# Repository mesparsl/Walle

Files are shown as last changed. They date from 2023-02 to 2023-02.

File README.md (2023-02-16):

# Walle
El wall-e es nuestro proyecto final nos hemos basado en este wall-e que encontramos por internet https://3dwork.io/wall-e-replica-impresion-3d/
!

[image](https://user-images.githubusercontent.com/124558681/219344904-b29a2cb5-0929-498d-a3b3-13a339d1f519.png)







1. Código Arduino (wall-e)

Programa principal para controlar los motores y servos del robot. Las características incluyen:

Una cola de animación, que realiza un seguimiento de los próximos movimientos de servo que el robot debe realizar.

Un generador de movimiento aleatorio, que permite que el robot se mueva de forma autónoma y parezca animado.

Control de velocidad de todos los servomotores, facilitando aceleraciones y desaceleraciones suaves.

Análisis en serie sin bloqueo, que permite el control remoto de los movimientos del robot.

Supervisión del nivel de la batería mediante un circuito divisor de potencial.

2. Servidor web Raspberry Pi (interfaz_web)

La interfaz web está programada en Python y utilizaMatraz para generar un servidor. La Raspberry Pi se conecta a través de USB al microcontrolador Arduino. Las características principales son:

Un joystick JavaScript, con el que se puede controlar fácilmente el movimiento del robot.

Control manual de todos los servomotores.

Una lista de animaciones de movimiento que puede realizar el robot.

Una lista de sonidos que se pueden reproducir.

Página de configuración, donde se pueden modificar los parámetros del motor, el volumen del sonido y las opciones de video.

Soporte para mando de juegos; en cualquier navegador moderno, puede usar un controlador Xbox o PlayStation conectado para controlar el robot.

Una página de inicio de sesión simple para evitar que todos tengan acceso a los controles (nota: este no es un sistema de control de acceso completo, no use esta interfaz web en redes públicas/no confiables)
 
 Imagen de la interfaz web y el robot. 
 
Instrucciones de configuración

1.Arduino

[a] Instalación básica

Asegúrese de que el cableado de la electrónica coincida con el diagrama que se muestra a continuación.

Descarga/clona la carpeta "wall-e" del repositorio de GitHub.

Abierto wall-e.ino en el IDE de Arduino; Los archivos animaciones.ino, MotorController.hpp y Cola.hpp también debería abrirse automáticamente en pestañas separadas del IDE.

Instala el Adafruit _ PWM Servo Driver.h biblioteca

Vaya a Sketch -> Incluir biblioteca -> Administrar bibliotecas...

BuscarServidor de Adafruit.

Instale la última versión de la biblioteca.

Conéctese a la computadora al microcontrolador con un cable USB. Asegúrese de que la correcta Junta y Puerto se seleccionan en el Herramientas menú.

Cargue el boceto en el microcontrolador.

Diagrama que muestra el cableado de los componentes electrónicos del robot.

[b] Prueba del programa principal



Una vez que el boceto se haya cargado en el Arduino, encienda la batería de 12 V mientras el microcontrolador aún está conectado a la computadora.

Abre el monitor de serie (botón en la parte superior derecha de Arduino IDE). Establezca la velocidad en baudios en 115200.

Para controlar el movimiento del robot, envía los caracteres 'w', 'a', 's' o 'd' para avanzar, izquierda, atrás o derecha respectivamente. Envía 'q' para detener todo movimiento.

Para mover la cabeza, envía los caracteres 'j', 'l', 'i' o 'k' para inclinar la cabeza hacia la izquierda o hacia la derecha y los ojos hacia arriba o hacia abajo. En esta etapa, los servos pueden intentar moverse más de lo debido y pueden parecer descoordinados. Esto se resolverá realizando los pasos de calibración del servomotor a continuación.

[c] Calibración del servomotor

Descarga/clona la carpeta "wall-e_calibration" del repositorio de GitHub

Abierto wall-e_calibration.ino en el IDE de Arduino.

Cargue el boceto en el microcontrolador, abra el monitor serie y establezca la velocidad de transmisión en 115200.

El esquema se usa para calibrar las longitudes de pulso PWM máximas y mínimas requeridas para mover cada servomotor en su rango de movimiento deseado. Las posiciones estándar BAJA y ALTA de cada uno de los servos se pueden ver en los diagramas en mi sitio web.

Al iniciar el boceto y abrir el monitor serie, debe aparecer un mensaje después de 2-3 segundos, diciendo que está listo para calibrar la posición BAJA del primer servomotor (la rotación del cabezal).

Envía el carácter 'a' y 'd' para mover el motor hacia adelante y hacia atrás en -10 y +10. Para un control más preciso, utilice los caracteres 'z' y 'c' para mover el motor en -1 y +1.

Una vez que el motor esté en la posición correcta, envíe el carácter 'n' para continuar con el paso de calibración. Pasará a la posición ALTA del mismo servo, después de lo cual el proceso se repetirá para cada uno de los 7 servos del robot.

Cuando todas las articulaciones estén calibradas, el boceto generará una matriz que contiene los valores de calibración en el monitor en serie.

Copie la matriz y péguela en lineas 144 al 150 del programawall-e.ino. La matriz debería verse similar a esto:



2. Servidor web Raspberry Pi

[a] Instalación básica

Configure Raspberry Pi para ejecutar la última versión de Raspberry Pi OS (Raspbian) - Full. Las instrucciones de configuración se pueden encontrar en el sitio web de frambuesa pi.

Abra la terminal de línea de comandos en la Raspberry Pi.

Asegúrese de que la lista de paquetes se haya actualizado (esto puede llevar algún tiempo):sudo apt update

Instalar Matraz - este es un marco de Python utilizado para crear servidores web:

Asegúrese de que pip esté instalado:sudo apt-get install python3-pip

Instale Flask y sus dependencias:sudo apt-get install python3-flask

sudo apt install git libsdl1.2-dev

sudo apt install git libsdl-mixer1.2-dev

sudo pip3 instalar pygame pyserial

Clone el repositorio en el directorio de inicio de Raspberry Pi:

cd ~
git clone https://github.com/chillibasket/walle-replica.git

Configure la contraseña del servidor web:

nano ~/walle-replica/web_interface/app.py

En línea26 deapp.py donde esta dice put_password_here, inserte la contraseña que desea utilizar para la interfaz web.

(Opcional) Cambie el directorio de audio predeterminado y la ubicación de la secuencia de comandos utilizada para iniciar/detener la transmisión de video.

Si siguió exactamente los pasos anteriores, no hay necesidad de hacerlo. Sin embargo, si desea mover los archivos de la interfaz web a un directorio diferente en Raspberry Pi, deberá cambiar la ubicación donde el programa buscará los archivos de audio.

En línea29 de app.py, escriba el directorio donde se encuentran los archivos de audio. Asegúrese de que la ubicación del directorio termine con una barra diagonal:/.

En línea28 de app.py, se puede modificar la ubicación del script utilizado para iniciar y detener la transmisión de la cámara de video.

Conéctese al Arduino/microcontrolador:

Conecte el Arduino/microcontrolador al puerto USB de la Raspberry Pi.

Si desea que el puerto serie utilizado por Arduino se seleccione de forma predeterminada en la interfaz web, puede configurar un dispositivo de puerto serie preferido en el código. ir a la línea27 deapp.py y reemplace el texto "ARDUINO" con el nombre de su dispositivo. El nombre debe coincidir con el que aparece en el menú desplegable en la pestaña "Configuración" de la interfaz web.

Para hacer que la interfaz se conecte automáticamente al Arduino cuando se inicia, puede cambiar la línea31 aautoStartArduino = Verdadero

Prensa CTRL+O para ahorrar yCTRL + X para salir del editor nano.

[b] Uso del servidor web

Para determinar la dirección IP actual de Raspberry Pi en su red, escriba el comando: hostname -I

Para iniciar el servidor:python3 ~/walle-réplica/web_interface/app.py

Para acceder a la interfaz web, abra un navegador en cualquier computadora/dispositivo en la misma red y escriba la dirección IP de la Raspberry Pi, siga por:5000. Por ejemplo192.168.1.10:5000

Para detener el servidor presione:CTRL + C

Para comenzar a controlar el robot, primero debe iniciar la comunicación en serie con el Arduino. Para ello, acceda a laAjustes pestaña de la interfaz web, seleccione el puerto serie correcto de la lista desplegable y presione en elreconectar botón.







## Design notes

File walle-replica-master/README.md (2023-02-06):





# Wall-E Robot Replica
Robot and controller code for a Wall-E replica robot. For more information about the robot, visit https://wired.chillibasket.com/3d-printed-wall-e/

<br />
<br />

## 1. Arduino Code (wall-e)
Main program to control the motors and servos of the robot. Features include:
1. An animation queue, keeping track of the next servo movements the robot needs to perform.
1. A random movement generator, allowing the robot to autonomously move and appear animated.
1. Velocity control of all servo motors, facilitating smooth accelerations and decelerations. 
1. Non-blocking serial parsing, allowing the movements of the robot to be remote controlled.
1. Battery level monitoring using a potential divider circuit.
<br />

## 2. Raspberry Pi Web Server (web_interface)
The web interface is programmed in Python and uses *Flask* to generate a server. The Raspberry Pi is connected via USB to the Arduino micro-controller. The main features are:
1. A JavaScript joystick, with which the movement of the robot can easily be controller.
1. Manual control of all the servo motors.
1. A list of movement animations which can be performed by the robot.
1. A list of sounds which can be played.
1. Settings page, where motor parameters, sound volume, and video options can be modified.
1. Gamepad support; on any modern browsers, you can use a connected Xbox of PlayStation controller to control the robot.
1. A simple login page to prevent everyone from having access to the controls (note: this is not a full access control system, please don't use this web interface on untrusted/public networks)

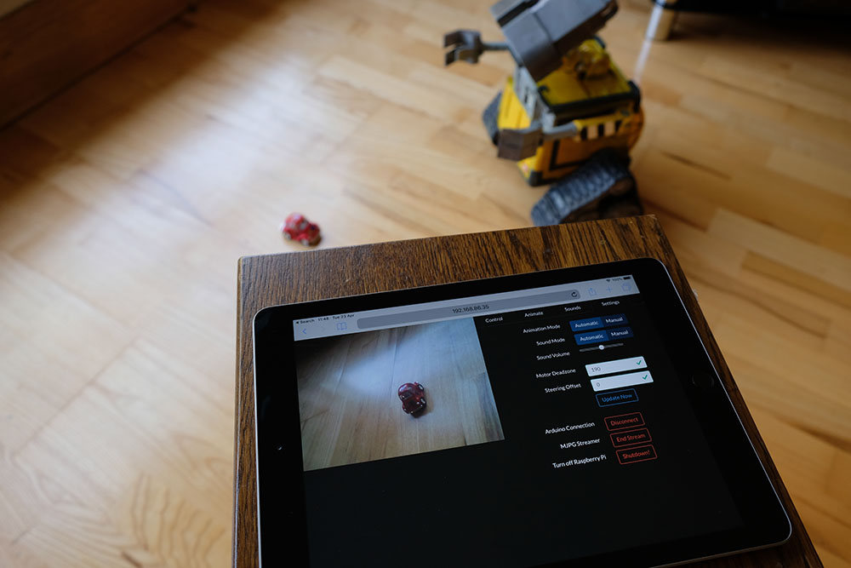
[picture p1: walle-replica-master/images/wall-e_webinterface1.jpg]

*Image of the web interface and robot*

<br />
<br />

## Setup Instructions

### 1. Arduino

#### [a] Basic Installation
1. Ensure that the wiring of the electronics matches the diagram shown below.
1. Download/clone the folder "wall-e" from the GitHub repository.
1. Open `wall-e.ino` in the Arduino IDE; the files `animations.ino`, `MotorController.hpp` and `Queue.hpp` should automatically open on separate tabs of the IDE as well.
1. Install the `Adafruit_PWMServoDriver.h` library
	1. Go to Sketch -> Include Library -> Manage Libraries...
	1. Search for *Adafruit Servo*.
	1. Install latest version of the library.
1. Connect to the computer to the micro-controller with a USB cable. Ensure that the correct *Board* and *Port* are selected in the *Tools* menu.
1. Upload the sketch to the micro-controller.

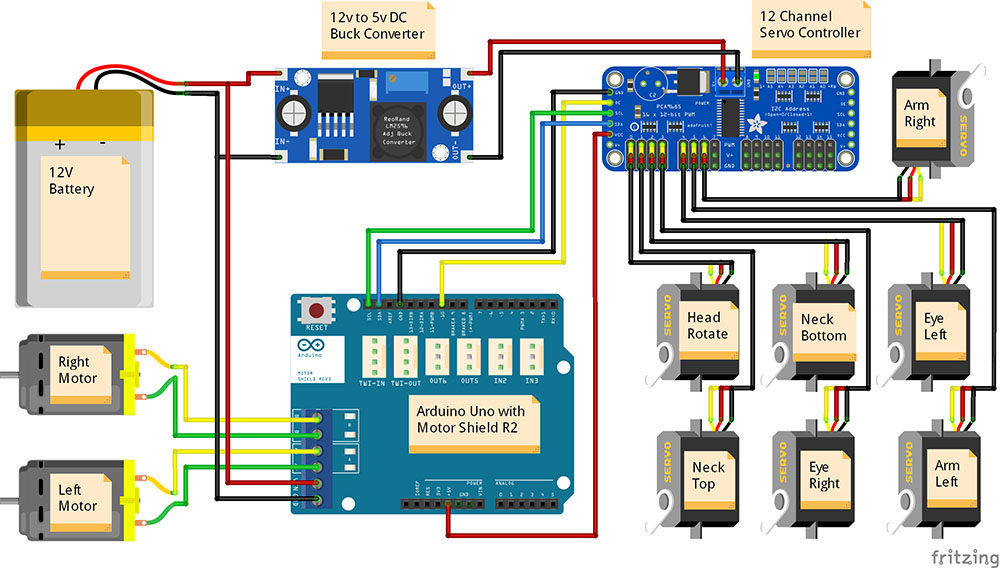
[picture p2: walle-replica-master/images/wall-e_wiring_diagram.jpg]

*Diagram showing the wiring of the robot's electronic components*
<br />

<br />

#### [b] Testing the Main Program
1. Once the sketch has been uploaded to the Arduino, power on the 12V battery while the micro-controller is still connected to the computer.
1. Open the *Serial Monitor* (button in top-right of Arduino IDE). Set the baud rate to 115200.
1. To control the movement of the robot, send the characters 'w', 'a', 's' or 'd' to move forward, left, back or right respectively. Send 'q' to stop all movement.
1. To move the head, send the characters 'j', 'l', 'i' or 'k' to tilt the head left or right and the eyes upwards or downwards. At this stage, the servos may try to move further than they should and may look uncoordinated. This will be solved by performing the servo motor calibration steps below.

<br />

#### [c] Servo Motor Calibration
1. Download/clone the folder "wall-e_calibration" from the GitHub repository
1. Open `wall-e_calibration.ino` in the Arduino IDE.
1. Upload the sketch to the micro-controller, and open the serial monitor and set the baud rate to 115200.
1. The sketch is used to calibrate the maximum and minimum PWM pulse lengths required to move each servo motor across its desired range of motion. The standard LOW and HIGH positions of each of the servos can be seen on diagrams [on my website](https://wired.chillibasket.com/3d-printed-wall-e/). 
1. When starting the sketch and opening the serial monitor, the a message should appear after 2-3 seconds, saying that it is ready to calibrate the LOW position of the first servo motor (the head rotation).
1. Send the character 'a' and 'd' to move the motor backwards and forwards by -10 and +10. For finer control, use the characters 'z' and 'c' to move the motor by -1 and +1. 
1. Once the motor is position in the correct position, send the character 'n' to proceed to the calibration step. It will move on to the HIGH position of the same servo, after which the process will repeat for each of the 7 servos in the robot.
1. When all joints are calibrated, the sketch will output an array containing the calibration values to the serial monitor.
1. Copy the array, and paste it into [lines 144](https://github.com/chillibasket/walle-replica/blob/master/wall-e/wall-e.ino#L144) to 150 of the program *wall-e.ino*. The array should look similar to this:
    ```cpp
    int preset[][2] =  {{410,120},  // head rotation
                        {532,178},  // neck top
                        {120,310},  // neck bottom
                        {465,271},  // eye right
                        {278,479},  // eye left
                        {340,135},  // arm left
                        {150,360}}; // arm right
    ```

<br />

#### [d] Battery Level Detection (Optional)
When using batteries to power the robot, it is important to keep track of how much power is left. Some batteries may break if they are over-discharged, and the SD card of the Raspberry Pi may become corrupted if not enough power is delivered.
1. To use the battery level detection feature on the Arduino, connect the following resistors and wiring as shown in the image below. The resistors (potential divider) reduce the 12V voltage down to a value below 5V, which is safe for the Arduino to measure using its analogue pins. The recommended resistor values are `R1 = 100kΩ` and `R2 = 47kΩ`.
1. Uncomment [line 54](https://github.com/chillibasket/walle-replica/blob/master/wall-e/wall-e.ino#L54) `#define BAT_L` in the main Arduino sketch *wall-e.ino*.
1. If you are using different resistor values, change the value of the potential divider gain factor on line 54 of the sketch, according to the formula: `POT_DIV = R2 / (R1 + R2)`. 
1. The program should now automatically check the battery level every 10 seconds, and this level will be shown on the Raspberry Pi web-interface in the "Status" section.

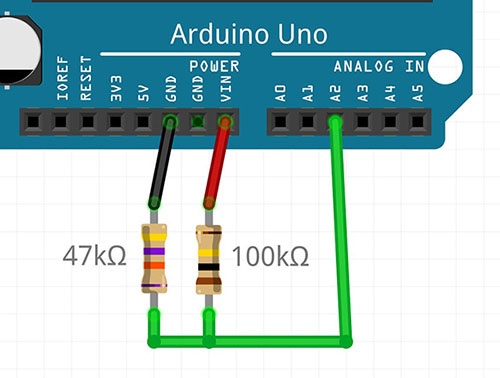
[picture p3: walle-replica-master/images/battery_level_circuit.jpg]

<br />
*Diagram showing the wiring of the battery level detection circuit*

<br />

#### [e] oLed Display (Optional) (Contributed by: [hpkevertje](https://github.com/hpkevertje))
It is possible to integrate a small oLED display which will show the battery level of the robot on the front battery indicator panel. This feature requires the battery level detection circuit in the previous section to be enabled, and the screen will update every time the battery level is calculated. This function uses the u8g2 display library in page mode; on the Arduino UNO you may get a warning that the memory usage is high, but this warning can be ignored. 
1. To use the oLed display feature on the Arduino, connect an i2c oLed display on the i2c bus on the servo motor module (see diagram).
1. Install the U8g2 library in the Arduino library manager:
    1. Go to Sketch -> Include Library -> Manage Libraries...
    1. Search for *U8gt*. The library publisher is "oliver".
    1. Install latest version of the library.
1. Uncomment [line 74](https://github.com/chillibasket/walle-replica/blob/master/wall-e/wall-e.ino#L74) `#define OLED` in the main Arduino sketch *wall-e.ino*.
1. If you are using a different display that is supported by the library, you can change the constructor on [line 78](https://github.com/chillibasket/walle-replica/blob/master/wall-e/wall-e.ino#L78) as documented on the [library reference page](https://github.com/olikraus/u8g2/wiki/u8g2setupcpp#constructor-reference). The default is for an SH1106_128X64_NONAME display.

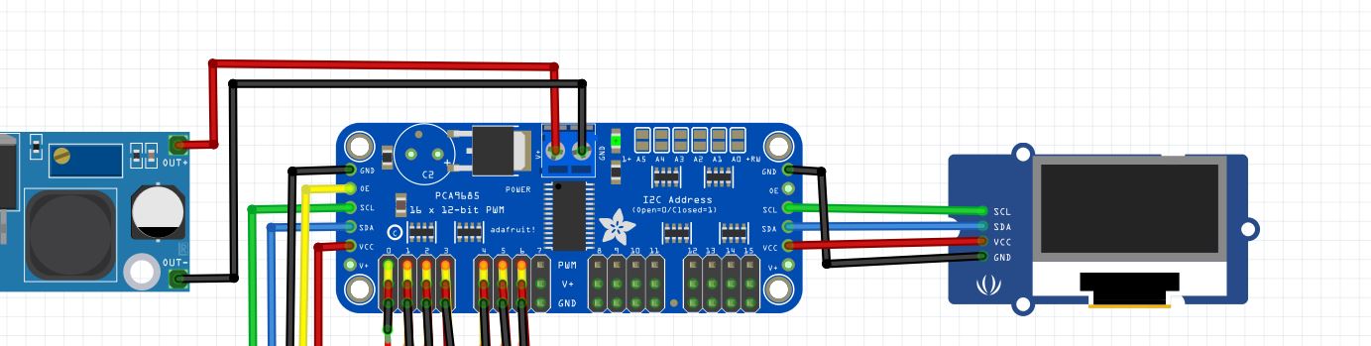
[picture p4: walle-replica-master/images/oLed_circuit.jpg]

<br />
*Diagram showing the wiring of the oLed display*

<br />

#### [f] Adding your own Servo Animations (Optional)
My code comes with two animations which replicate scenes from the movie; the eye movement Wall-E does when booting-up, and a sequence of motions as Wall-E inquisitively looks around. From version 2.7 of the code, I've now made it easier to add your own servo motor animations so that you can make your Wall-E do other movements...
1. Open up the file `animations.ino`, which is located in the same folder as the main Arduino sketch. 
1. Each animation command consists of the positions you want each of the servo motors to move to, and the amount of time the animation should wait until moving on to the next instruction.
1. You can add a new animation by inserting an extra `case` section into the switch statement. You should slot your extra code into the space above the `default` section. For example:
    ```cpp
    case 3:
            // --- Title of your new motion sequence ---
            //          time,head,necT,necB,eyeR,eyeL,armL,armR
            queue.push({  12,  48,  40,   0,  35,  45,  60,  59});
            queue.push({1500,  48,  40,  20, 100,   0,  80,  80});
            // Add as many additional movements here as you need to complete the animation
            // queue.push({time, head rotation, neck top, neck bottom, eye right, eye left, arm left, arm right})
            break;
    ```
1. The time needs to be a number in milliseconds (for example, 3.5 seconds = 3500)
1. The servo motor position commands need to be an integer number between 0 to 100, where `0 = LOW` and `100 = HIGH` servo position as calibrated in the `wall-e_calibration.ino` sketch.
1. If you want to disable a motor for a specific move, you can use -1. 

<br />
<br />

### 2. Raspberry Pi Web Server

#### [a] Basic Installation
1. Setup the Raspberry Pi to run the latest version of Raspberry Pi OS (Raspbian) - Full. The setup instructions can be found on the [Raspberry Pi website](https://www.raspberrypi.org/documentation/installation/installing-images/).
1. Open the command line terminal on the Raspberry Pi.
1. Ensure that the package list has been updated (this may take some time): `sudo apt update`
1. Install *Flask* - this is a Python framework used to create web servers:
    1. Ensure that pip is installed: `sudo apt install python3-pip`
    1. Install Flask and its dependencies: `sudo pip3 install flask`
1. (Optional) The *Full* version of Raspbian includes these packages by default, but if you are using a different OS (for example the *Lite* version), you will need to run these commands:
    ```shell
    sudo apt install git libsdl1.2 libsdl-mixer1.2
    sudo pip3 install pygame pyserial
    ```
1. Clone repository into the home directory of the Raspberry Pi:
    ```shell
    cd ~
    git clone https://github.com/chillibasket/walle-replica.git
    ```
1. Set the web server password:
    1. Open *app.py*: `nano ~/walle-replica/web_interface/app.py` 
    1. On line [26](https://github.com/chillibasket/walle-replica/blob/master/web_interface/app.py#L26) of *app.py* where is says `put_password_here`, insert the password you want to use for the web interface.
1. (Optional) Change the default audio directory and location of the script used to start/stop the video stream.
    1. If you followed the steps above exactly, there is no need to do this. However, if you want to move the web-interface files to a different directory on the Raspberry Pi, you will need to change the location where the program will look for the audio files.
    1. On line [29](https://github.com/chillibasket/walle-replica/blob/master/web_interface/app.py#L29) of *app.py*, type the directory where the audio files are located. Ensure that the directory location ends with a forward slash: `/`.
    1. On line [28](https://github.com/chillibasket/walle-replica/blob/master/web_interface/app.py#L28) of *app.py*, the location of the script used to start and stop the video camera stream can be modified.
1. Connect to the Arduino/micro-controller:
    1. Plug the Arduino/micro-controller into the USB port of the Raspberry Pi.
    1. If you would like the serial port used by the Arduino to be selected by default in the web-interface, you can set a preferred serial port device in the code. Go to line [27](https://github.com/chillibasket/walle-replica/blob/master/web_interface/app.py#L26) of *app.py* and replace the text "ARDUINO" with the name of your device. The name must match the one which appears in the drop-down menu in the "Settings" tab of the web-interface.
    1. To make the interface automatically connect to the Arduino when it starts up, you can change line [31](https://github.com/chillibasket/walle-replica/blob/master/web_interface/app.py#L31) to `autoStartArduino = True`
    1. Press `CTRL + O` to save and `CTRL + X` to exit the nano editor.

<br />

#### [b] Using the Web Server
1. To determine the current IP address of the Raspberry Pi on your network, type the command: `hostname -I`
1. To start the server: `python3 ~/walle-replica/web_interface/app.py`
1. To access the web interface, open a browser on any computer/device on the same network and type in the IP address of the Raspberry Pi, follow by `:5000`. For example `192.168.1.10:5000`
1. To stop the server press: `CTRL + C`
1. To start controlling the robot, you first need to start serial communication with the Arduino. To do this, go to the `Settings` tab of the web-interface, select the correct serial port from the drop-down list and press on the `Reconnect` button.

<br />

#### [c] Adding a Camera Stream (Optional)
1. If you are using the Official Raspberry Pi camera, you will first need to enable the camera in `sudo raspi-config`. In the config screen which appears, navigate to “Interface Options” > “Camera” > “Enable”.
1. Install *mjpg-streamer* - this is used to stream the video to the webserver. The steps below are based on the instructions [described here](https://github.com/cncjs/cncjs/wiki/Setup-Guide:-Raspberry-Pi-%7C-MJPEG-Streamer-Install-&-Setup-&-FFMpeg-Recording) for the CNC JS project. To install the required libraries, run all of the following commands:
    ```bash
    # Update & Install Tools
    sudo apt-get update -y
    sudo apt-get upgrade -y
    sudo apt-get install build-essential git imagemagick libv4l-dev libjpeg-dev cmake -y

    # Clone Repo in /tmp
    cd /tmp
    git clone https://github.com/jacksonliam/mjpg-streamer.git
    cd mjpg-streamer/mjpg-streamer-experimental

    # Make
    make
    sudo make install
    
    ```
1. Create a new script which will be used to start and stop the camera stream: `nano ~/mjpg-streamer.sh`
1. Paste the following code into the script file; you can modify the settings frame rate, quality and resolution to suit the camera you are using:
    ```bash
    #!/bin/bash
    # chmod +x mjpg-streamer.sh
    # Crontab: @reboot /home/pi/mjpg-streamer/mjpg-streamer.sh start
    # Crontab: @reboot /home/pi/mjpg-streamer/mjpg-streamer-experimental/mjpg-streamer.sh start

    MJPG_STREAMER_BIN="/usr/local/bin/mjpg_streamer"  # "$(dirname $0)/mjpg_streamer"
    MJPG_STREAMER_WWW="/usr/local/share/mjpg-streamer/www"
    MJPG_STREAMER_LOG_FILE="${0%.*}.log"  # "$(dirname $0)/mjpg-streamer.log"
    RUNNING_CHECK_INTERVAL="2" # how often to check to make sure the server is running (in seconds)
    HANGING_CHECK_INTERVAL="3" # how often to check to make sure the server is not hanging (in seconds)

    VIDEO_DEV="/dev/video0"
    FRAME_RATE="5"
    QUALITY="80"
    RESOLUTION="1280x720"  # 160x120 176x144 320x240 352x288 424x240 432x240 640x360 640x480 800x448 800x600 960x544 1280x720 1920x1080 (QVGA, VGA, SVGA, WXGA)   #  lsusb -s 001:006 -v | egrep "Width|Height" # https://www.textfixer.com/tools/alphabetical-order.php  # v4l2-ctl --list-formats-ext  # Show Supported Video Formates
    PORT="8080"
    YUV="true"

    ################INPUT_OPTIONS="-r ${RESOLUTION} -d ${VIDEO_DEV} -f ${FRAME_RATE} -q ${QUALITY} -pl 60hz"
    INPUT_OPTIONS="-r ${RESOLUTION} -d ${VIDEO_DEV} -q ${QUALITY} -pl 60hz --every_frame 2"  # Limit Framerate with  "--every_frame ", ( mjpg_streamer --input "input_uvc.so --help" )

    if [ "${YUV}" == "true" ]; then
        INPUT_OPTIONS+=" -y"
    fi

    OUTPUT_OPTIONS="-p ${PORT} -w ${MJPG_STREAMER_WWW}"

    # ==========================================================
    function running() {
        if ps aux | grep ${MJPG_STREAMER_BIN} | grep ${VIDEO_DEV} >/dev/null 2>&1; then
            return 0

        else
            return 1

        fi
    }

    function start() {
        if running; then
            echo "[$VIDEO_DEV] already started"
            return 1
        fi

        export LD_LIBRARY_PATH="$(dirname $MJPG_STREAMER_BIN):."

        echo "Starting: [$VIDEO_DEV] ${MJPG_STREAMER_BIN} -i \"input_uvc.so ${INPUT_OPTIONS}\" -o \"output_http.so ${OUTPUT_OPTIONS}\""
        ${MJPG_STREAMER_BIN} -i "input_uvc.so ${INPUT_OPTIONS}" -o "output_http.so ${OUTPUT_OPTIONS}" >> ${MJPG_STREAMER_LOG_FILE} 2>&1 &

        sleep 1

        if running; then
            if [ "$1" != "nocheck" ]; then
                check_running & > /dev/null 2>&1 # start the running checking task
                check_hanging & > /dev/null 2>&1 # start the hanging checking task
            fi

            echo "[$VIDEO_DEV] started"
            return 0

        else
            echo "[$VIDEO_DEV] failed to start"
            return 1

        fi
    }

    function stop() {
        if ! running; then
            echo "[$VIDEO_DEV] not running"
            return 1
        fi

        own_pid=$$

        if [ "$1" != "nocheck" ]; then
            # stop the script running check task
            ps aux | grep $0 | grep start | tr -s ' ' | cut -d ' ' -f 2 | grep -v ${own_pid} | xargs -r kill
            sleep 0.5
        fi

        # stop the server
        ps aux | grep ${MJPG_STREAMER_BIN} | grep ${VIDEO_DEV} | tr -s ' ' | cut -d ' ' -f 2 | grep -v ${own_pid} | xargs -r kill

        echo "[$VIDEO_DEV] stopped"
        return 0
    }

    function check_running() {
        echo "[$VIDEO_DEV] starting running check task" >> ${MJPG_STREAMER_LOG_FILE}

        while true; do
            sleep ${RUNNING_CHECK_INTERVAL}

            if ! running; then
                echo "[$VIDEO_DEV] server stopped, starting" >> ${MJPG_STREAMER_LOG_FILE}
                start nocheck
            fi
        done
    }

    function check_hanging() {
        echo "[$VIDEO_DEV] starting hanging check task" >> ${MJPG_STREAMER_LOG_FILE}

        while true; do
            sleep ${HANGING_CHECK_INTERVAL}

            # treat the "error grabbing frames" case
            if tail -n2 ${MJPG_STREAMER_LOG_FILE} | grep -i "error grabbing frames" > /dev/null; then
                echo "[$VIDEO_DEV] server is hanging, killing" >> ${MJPG_STREAMER_LOG_FILE}
                stop nocheck
            fi
        done
    }

    function help() {
        echo "Usage: $0 [start|stop|restart|status]"
        return 0
    }

    if [ "$1" == "start" ]; then
        start && exit 0 || exit -1

    elif [ "$1" == "stop" ]; then
        stop && exit 0 || exit -1

    elif [ "$1" == "restart" ]; then
        stop && sleep 1
        start && exit 0 || exit -1

    elif [ "$1" == "status" ]; then
        if running; then
            echo "[$VIDEO_DEV] running"
            exit 0

        else
            echo "[$VIDEO_DEV] stopped"
            exit 1

        fi

    else
        help

    fi

    ```
1. Press `CTRL + O` to save and `CTRL + X` to exit the nano editor.
1. Make sure that the manager script you created has the correct name and is in the correct directory: `/home/pi/mjpg-streamer.sh`. If you want the save the script in a different location, you need to update line 22 of *app.py*.
1. To make the script executable by the web-server, run this command in the terminal: `chmod +x /home/pi/mjpg-streamer.sh`
1. If you want the camera to automatically startup when you open the web-interface you can change line [32](https://github.com/chillibasket/walle-replica/blob/master/web_interface/app.py#L32) of *app.py* to `autoStartCamera = True`

<br />

#### [d] Automatically start Server on Boot *(Optional, but recommended)*
1. Create a `.service` file which is used to start the web interface: `nano ~/walle.service`
1. Paste the following text into the file:
    ```text
    [Unit]
    Description=Start Wall-E Web Interface
    After=network.target

    [Service]
    WorkingDirectory=/home/pi/walle-replica/web_interface
    ExecStart=/usr/bin/python3 app.py
    Restart=always
    StandardOutput=syslog
    StandardError=syslog
    SyslogIdentifier=walle
    User=pi

    [Install]
    WantedBy=multi-user.target
    ```
1. Press `CTRL + O` to save and `CTRL + X` to exit the nano editor.
1. Copy this file into the startup directory using the command: `sudo cp ~/walle.service /etc/systemd/system/walle.service`
1. To enable auto-start, use the following command: `sudo systemctl enable walle.service`
1. The web interface should now automatically start when the Raspberry Pi is turned on. You can also manually start and stop the service using the commands: `sudo systemctl start walle.service` and `sudo systemctl stop walle.service` 

<br />

#### [e] Adding new Sounds (Optional)
1. By default the Raspberry should automatically select whether to output audio to the HDMI port or the headphone jack. However, you can ensure that it always uses the headphone jack with the following command: `amixer cset numid=3 1`
1. Make sure that all the sound files you want to use are of type `*.ogg`. Most music/sound editors should be able to convert the sound file to this format.
1. Change the file name so that it has the following format: `[group name]_[file name]_[length in milliseconds].ogg`. For example: `voice_eva_1200.ogg`. In the web-interface, the audio files will be grouped using the "group name" and sorted alphabetically.
1. Upload the sound file to Raspberry Pi in the following folder: `~/walle-replica/web_interface/static/sounds/`
1. All the files should appear in the web interface when you reload the page. If the files do not appear, you may need to change the privileges required to access the folder: `sudo chmod -R 755 ~/walle-replica/web_interface/static/sounds`

<br />

#### [f] Set up the Raspberry Pi as a WiFi hotspot *(Optional)*
If you would like to control the robot outdoors or at conventions, there may not be any safe WiFi networks you can connect to. To overcome this issue and eliminate the need for any external networking equipment, the Raspberry Pi can broadcast its own WiFi network. You can then connect the computer/phone/tablet you are using to control the robot directly to this network.

To set up the WiFi hotspot, we will use the [RaspAP project](https://raspap.com/) which takes care of all the configuration and tools to get the system working. The following instructions are based on their quick installation guide:

1. Update Raspian, the kernel and firmware (and then reboot):
    ```
    sudo apt-get update
    sudo apt-get dist-upgrade
    sudo reboot
    ```
1. Ensure that you have set the correct WiFi country in raspi-config’s Localisation Options: `sudo raspi-config`
1. Run the quick installer: `curl -sL https://install.raspap.com | bash`
    1. For the first few yes/no prompts which will appear during the install, type “y” (yes) to accept all of the recommended settings. The final two prompts (Ad Blocking and the next one) are not required so you can type “n” (no) for those.
1. Reboot the Raspberry Pi again to implement the changes: `sudo reboot`
1. Now the Raspberry Pi should be broadcasting a WiFi network with the following details:
    1. SSID (wifi name): `raspi-webgui`
    1. Password: `ChangeMe`
1. After connecting to the WiFi network from a your computer, phone or tablet, the Wall-E web-interface can be opened by typing this address into your browser: `http://10.3.141.1:5000`
1. (Recommended) To change the WiFi name and password, go to the WiFi configuration webpage at: `http://10.3.141.1`. The default username is `admin` and password is `secret`.
    1. Click on “Hotspot” in the left sidebar. In the “Basic” tab you can change the WiFi network name, while the WiFi password can be changed in the “Security” tab.
    1. To change the admin password for the interface used to manage the WiFi settings, click on the “Admin” icon in the top-right of the interface.

<br />
<br />

## Changelog

#### 31st October 2021 (Version 2.92)
1. Added options in *app.py* to automatically connect to the Arduino and to start the camera stream when the web-interface is opened for the first time.

#### 30th October 2021 (Version 2.91)
1. Changed camera stream port from 8081 to 8080 inline with changes made to the start/stop script.
1. Improved the camera setup instructions, listing all steps explicitly rather than linking to an external repository.

#### 29th May 2021 (Version 2.9)
1. Improved code commenting and variable/parameter naming to make it easier to understand.
1. Fixed bugs related to motor deadzone and trim parameters.

#### 21st March 2021 (Version 2.8)
1. Updated instructions of how to use an oLed display. 

#### 19th December 2020
1. Updated instructions of how to set up a WiFi hotspot on the Raspberry Pi. 
1. Added offline Lato font files to prevent errors when running the web-interface while disconnected from the internet.

#### 7th August 2020 (Version 2.7)
1. Added a soft servo start function to the main Wall-E sketch and the servo calibration sketch. This prevents the servos from jumping as violently on startup.
1. Changed the data-type of the animation queue to reduce the amount of dynamic memory required. Also updated the Queue class so that the buffer memory can be declared globally; this means the compiler can keep track of how much memory the queue actually uses.
1. Moved the preset servo animations into a separate file, to make it easier to add your own animations. 

#### 20th June 2020
1. Minor bug fixes of the `Queue.hpp` and `MotoController.hpp` classes.
1. Updated commenting of code to make it more consistent.

#### 16th February 2020
1. Added gamepad support; any controller can now be used (such as the Xbox or PlayStation controllers) to puppet the robot.
1. Improved serial port handling; in the settings tab, all of the available serial ports are listed in a drop-down menu. 
1. New status indicators are now shown below the video stream. They visualise whether the Arduino and/or gamepad are connected.
1. Added support for battery level detection in both the Arduino code and the Raspberry Pi web interface.
1. Fixed the bug where the virtual joystick no longer worked properly when the window was resized.
1. Plus many other bug fixes!

#### 25th January 2020
1. Restructured the web-interface to make it display more nicely on mobile devices; fancy icons are now used!
1. Added manual servo control - this allows individual servos to be controlled directly from the web-interface.
1. Improved error handling - error messages are now consistently displayed in a pop-up at the bottom of the page.
1. Added instructions about how to automatically start server on boot to the Readme.

#### 31st October 2019
1. Fixed some bugs related to sound playback.
1. Added 2 sample sound files, which ensures that the sound directory is included in the git files.

#### 30th October 2019 
1. Added *wall-e_calibration.ino*, with which the maximum and minimum pulse widths of the servo motors can be calibrated.
1. Updated *wall-e.ino* to use relative coordinates rather than absolute servo pulse widths for the animation presets. This allows the servo calibration data to be used to ensure the movements are the same on all variants of the robot.

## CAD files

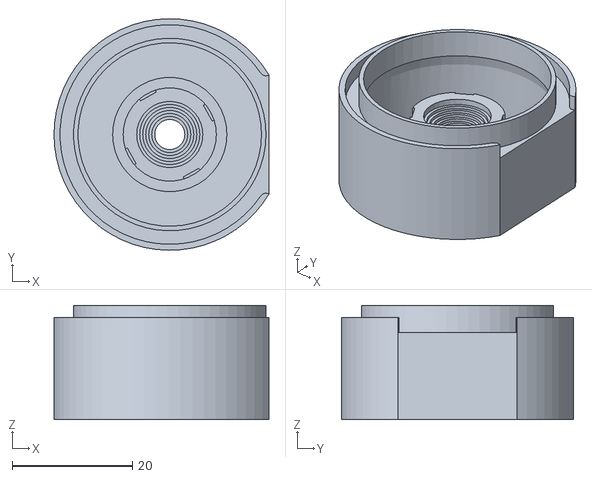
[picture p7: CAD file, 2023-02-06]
Wall-E STEP Files/eye-camera-replica.stl
35.8 x 38.5 x 19.0

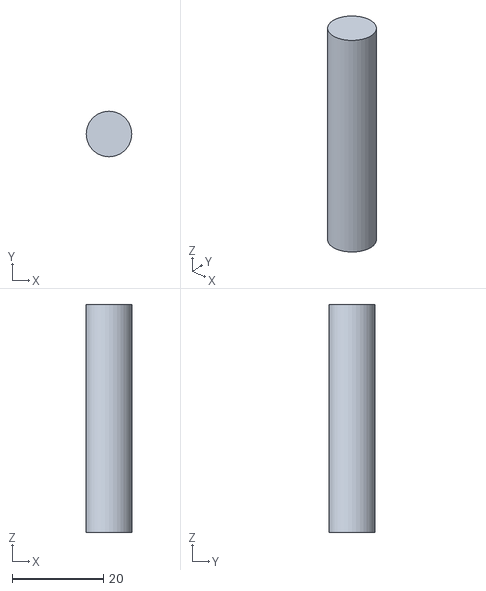
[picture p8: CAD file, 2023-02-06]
Wall-E STEP Files/hand-axle-x2.stl
10.0 x 10.0 x 50.0

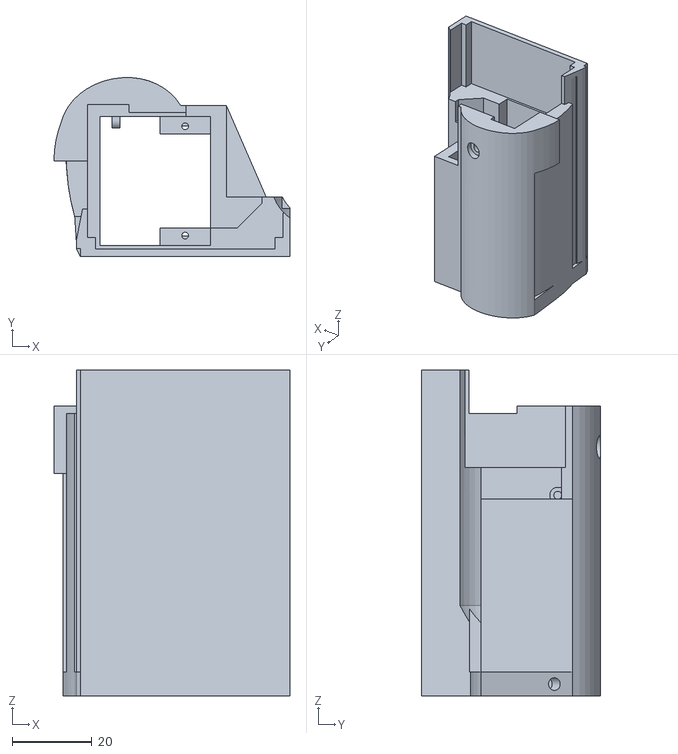
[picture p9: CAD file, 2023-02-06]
Wall-E STEP Files/eye-middle-right.stl
59.4 x 45.0 x 82.0

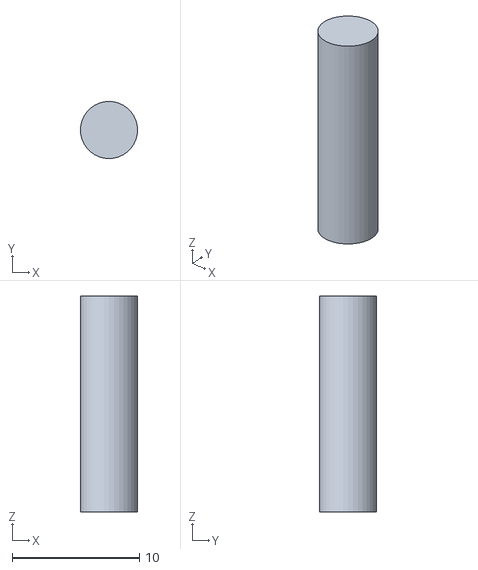
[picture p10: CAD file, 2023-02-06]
Wall-E STEP Files/body-front-pins-x2.stl
4.50 x 4.50 x 17.0

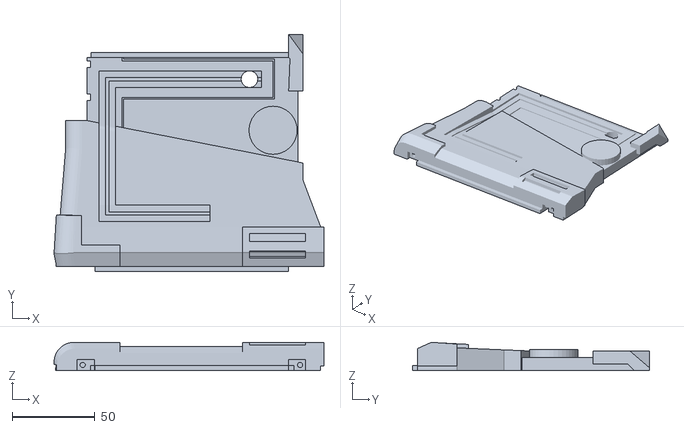
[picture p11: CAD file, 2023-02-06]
Wall-E STEP Files/body-left.stl
162.7 x 143.0 x 17.0

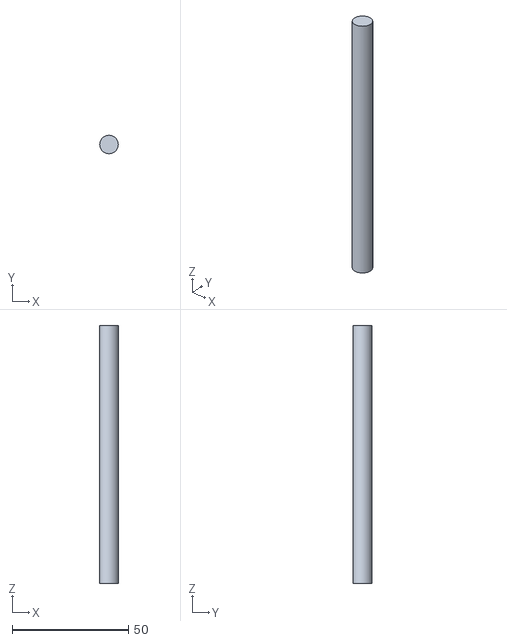
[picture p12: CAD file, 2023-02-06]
Wall-E STEP Files/head-axle.stl
8.00 x 8.00 x 111.0

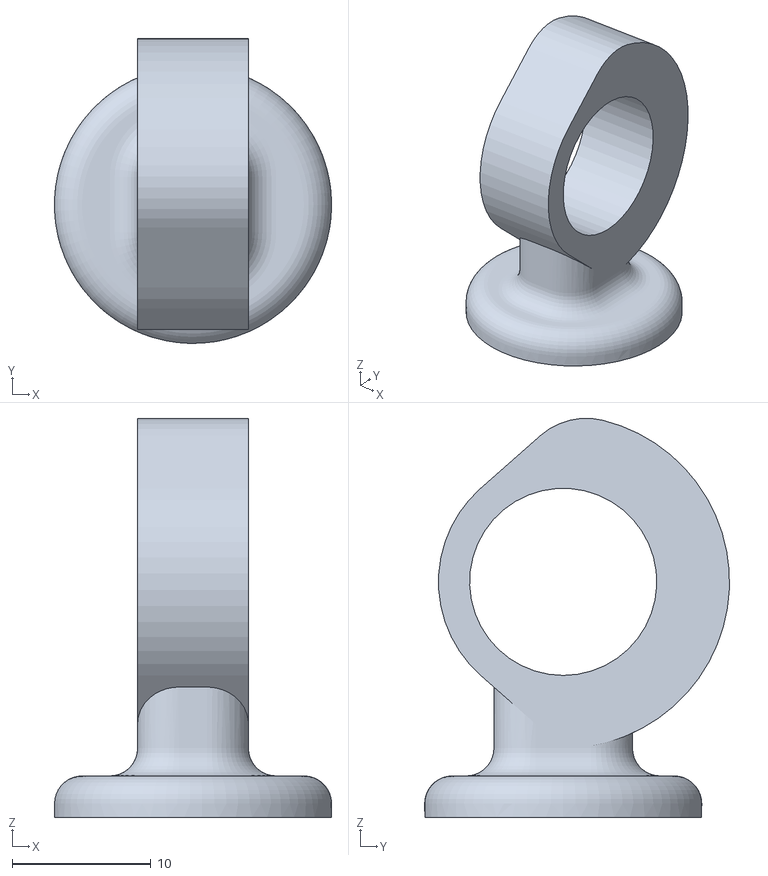
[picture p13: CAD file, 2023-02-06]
Wall-E STEP Files/arm-hinge-outer-x2.stl
20.0 x 22.0 x 28.8

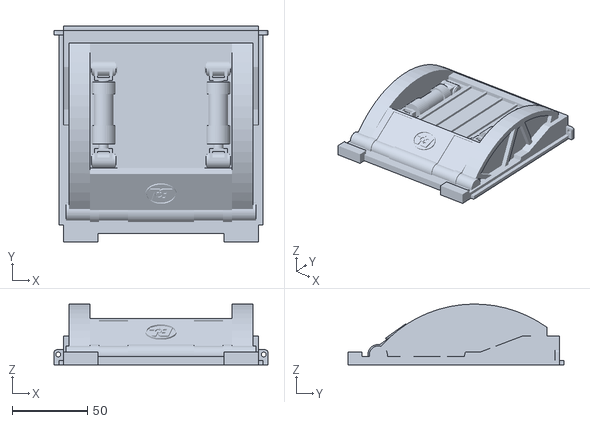
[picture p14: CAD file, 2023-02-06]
Wall-E STEP Files/body-back.stl
141.9 x 143.0 x 40.3

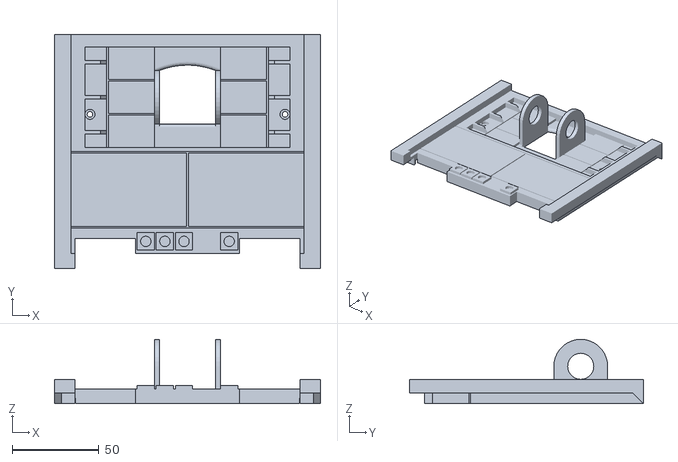
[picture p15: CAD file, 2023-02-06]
Wall-E STEP Files/body-top.stl
153.0 x 134.4 x 37.0

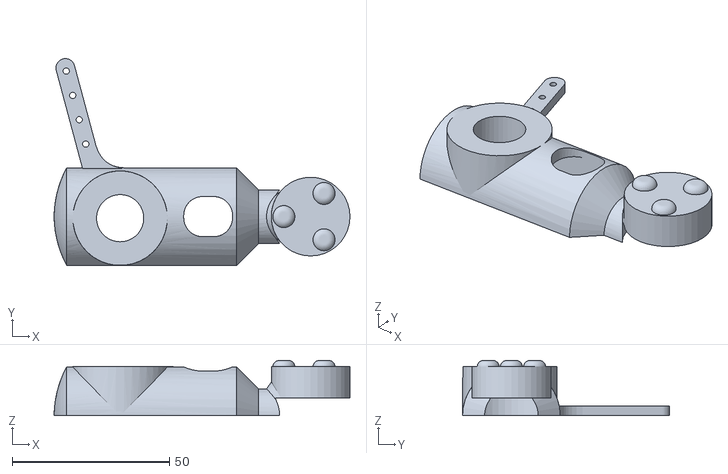
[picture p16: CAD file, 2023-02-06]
Wall-E STEP Files/neck-bottom-left.stl
94.0 x 65.7 x 17.5

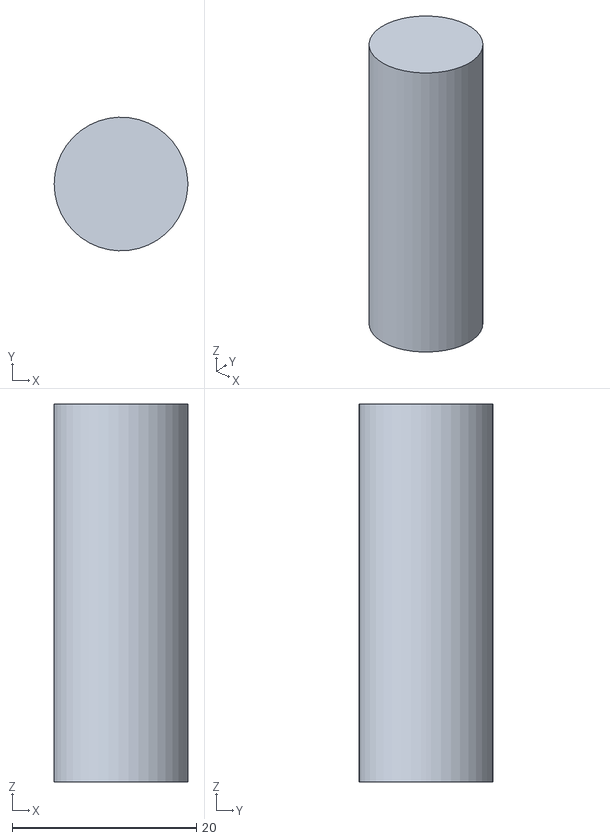
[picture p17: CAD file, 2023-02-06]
Wall-E STEP Files/neck-bottom-axle.stl
14.5 x 14.5 x 41.0

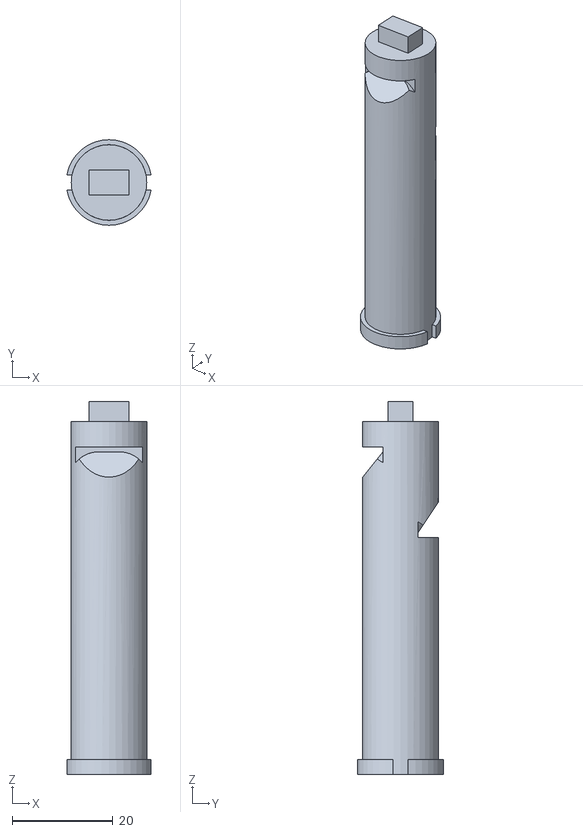
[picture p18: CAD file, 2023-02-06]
Wall-E STEP Files/arm-piston-x2.stl
16.7 x 17.0 x 74.0

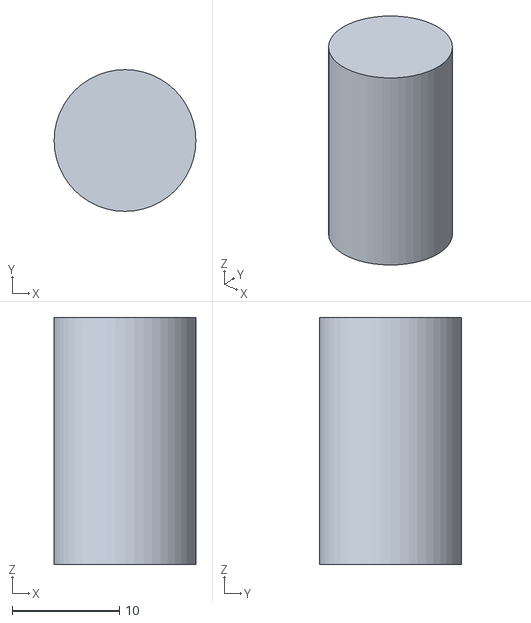
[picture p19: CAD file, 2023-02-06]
Wall-E STEP Files/arm-hinge-axle-x2.stl
13.2 x 13.2 x 23.0

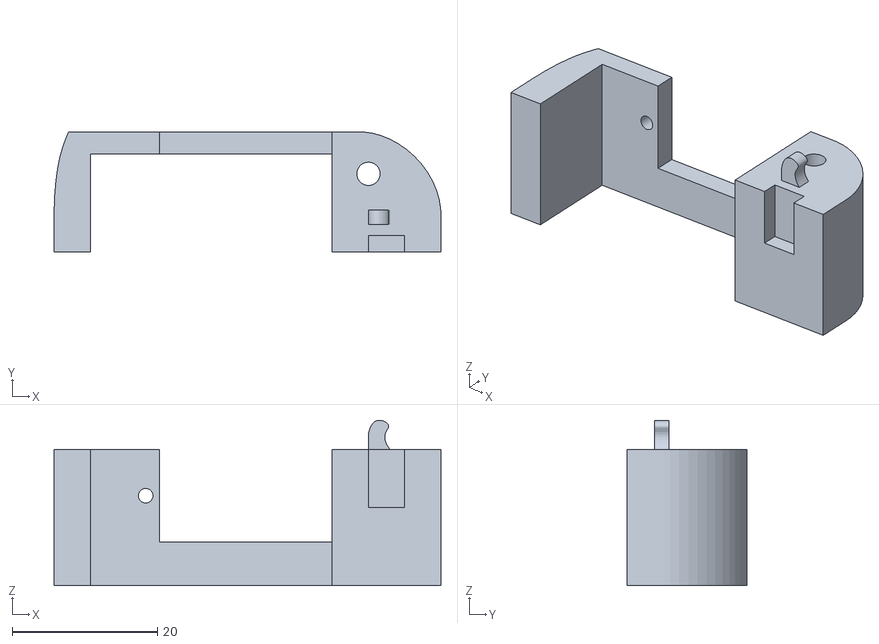
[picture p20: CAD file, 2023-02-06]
Wall-E STEP Files/arm-servo-bracket-left.stl
53.2 x 16.5 x 22.7

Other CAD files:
Wall-E STEP Files/eye-front-left.stl
Wall-E STEP Files/eye-camera-mount.stl
Wall-E STEP Files/hand-bracket-x2.stl
Wall-E STEP Files/arm-servo-bracket-right.stl
Wall-E STEP Files/arm-barrel-end-x2 (1).stl
Wall-E STEP Files/arm-barrel-x2 (1).stl
Wall-E STEP Files/arm-hinge-inner-x2.stl
Wall-E STEP Files/body-bottom.stl
Wall-E STEP Files/body-front-door.stl
Wall-E STEP Files/body-front.stl
Wall-E STEP Files/body-neck-servo-holder.stl
Wall-E STEP Files/body-right (1).stl
Wall-E STEP Files/body-right.stl
Wall-E STEP Files/eye-back-left.stl
Wall-E STEP Files/eye-back-right.stl
Wall-E STEP Files/eye-front-right.stl
Wall-E STEP Files/eye-middle-left.stl
Wall-E STEP Files/hand-finger-left-x2.stl
Wall-E STEP Files/hand-finger-middle-x2.stl
Wall-E STEP Files/hand-finger-right-x2.stl
Wall-E STEP Files/head-center.stl
Wall-E STEP Files/neck-bottom-linkage.stl
Wall-E STEP Files/neck-bottom-right.stl
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

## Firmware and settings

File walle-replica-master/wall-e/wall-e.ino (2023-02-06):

#include <Wire.h>
#include <Adafruit_PWMServoDriver.h>
#include "Queue.hpp"
#include "MotorController.hpp"


/// Define pin-mapping
// -- -- -- -- -- -- -- -- -- -- -- -- -- --
#define DIRECTION_L_PIN 12           // Motor direction pins
#define DIRECTION_R_PIN 13
#define PWM_SPEED_L_PIN  3           // Motor PWM pins
#define PWM_SPEED_R_PIN 11
#define BRAKE_L_PIN  9               // Motor brake pins
#define BRAKE_R_PIN  8
#define SERVO_ENABLE_PIN 10          // Servo shield output enable pin


/**
 * Battery level detection
 *
 *   .------R1-----.-------R2------.     | The diagram to the left shows the  |
 *   |             |               |     | potential divider circuit used by  |
 * V_Raw     Analogue pin A2      GND    | the battery level detection system |
 *
 * @note The scaling factor is calculated according to ratio of the two resistors:
 *       DIVIDER_SCALING_FACTOR = R2 / (R1 + R2)
 *       For example: 47000 / (100000 + 47000) = 0.3197
 *
 * To enable battery level detection, uncomment the next line:
 */
#define BAT_L
#ifdef BAT_L
	#define BATTERY_LEVEL_PIN A2
	#define BATTERY_MAX_VOLTAGE 12.6
	#define BATTERY_MIN_VOLTAGE 10.2
	#define DIVIDER_SCALING_FACTOR 0.3197


	/**
	 * OLED Battery Level Display
	 *
	 * Displays the battery level on an oLed display. Supports a 1.3 inch oLed display using I2C.
	 * The constructor is set to a SH1106 1.3 inch display. Change the constructor if you want to use a different display.
	 * 
	 * @note Requires Battery level detection to be enabled above
	 * @note You may get a "Low memory available" warning when compiling for Arduino UNO boards (79% memory usage).
	 *       It did work in my case, so you should be able to ignore this message.
	 *
	 * To enable the oLED display, uncomment the next line:
	 */
	#define OLED
	#ifdef OLED
	  
	  //#include <U8g2lib.h>
	  //U8G2_SH1106_128X64_NONAME_1_HW_I2C u8g2(U8G2_R0, 10);

	#endif /* OLED */
#endif /* BAT_L */


/// Define other constants
// -- -- -- -- -- -- -- -- -- -- -- -- -- --
#define NUMBER_OF_SERVOS 7        // Number of servo motors
#define SERVO_UPDATE_TIME 10      // Time in milliseconds of how often to update servo and motor positions
#define SERVO_OFF_TIME 6000       // Turn servo motors off after 6 seconds
#define STATUS_CHECK_TIME 10000   // Time in milliseconds of how often to check robot status (eg. battery level)
#define CONTROLLER_THRESHOLD 1    // The minimum error which the dynamics controller tries to achieve
#define MAX_SERIAL_LENGTH 5       // Maximum number of characters that can be received



/// Instantiate Objects
// -- -- -- -- -- -- -- -- -- -- -- -- -- --
// Servo shield controller class - assumes default address 0x40
Adafruit_PWMServoDriver pwm = Adafruit_PWMServoDriver();

// Set up motor controller classes
MotorController motorL(DIRECTION_L_PIN, PWM_SPEED_L_PIN, BRAKE_L_PIN, false);
MotorController motorR(DIRECTION_R_PIN, PWM_SPEED_R_PIN, BRAKE_R_PIN, false);

// Queue for animations - buffer is defined outside of the queue class
// so that the compiler knows how much dynamic memory will be used
struct animation_t {
	uint16_t timer;
	int8_t servos[NUMBER_OF_SERVOS]; 
};

#define QUEUE_LENGTH 40
animation_t buffer[QUEUE_LENGTH];
Queue <animation_t> queue(QUEUE_LENGTH, buffer);


/// Motor Control Variables
// -- -- -- -- -- -- -- -- -- -- -- -- -- --
int pwmspeed = 255;
int moveValue = 0;
int turnValue = 0;
int turnOffset = 0;
int motorDeadzone = 0;


/// Runtime Variables
// -- -- -- -- -- -- -- -- -- -- -- -- -- --
unsigned long lastTime = 0;
unsigned long animeTimer = 0;
unsigned long motorTimer = 0;
unsigned long statusTimer = 0;
unsigned long updateTimer = 0;
bool autoMode = false;


// Serial Parsing
// -- -- -- -- -- -- -- -- -- -- -- -- -- --
char firstChar;
char serialBuffer[MAX_SERIAL_LENGTH];
uint8_t serialLength = 0;


// ****** SERVO MOTOR CALIBRATION *********************
// Servo Positions:  Low,High
int preset[][2] =  {{410,120},  // head rotation
                    {532,178},  // neck top
                    {120,310},  // neck bottom
                    {465,271},  // eye right
                    {278,479},  // eye left
                    {340,135},  // arm left
                    {150,360}}; // arm right
// *****************************************************


// Servo Control - Position, Velocity, Acceleration
// -- -- -- -- -- -- -- -- -- -- -- -- -- --
// Servo Pins:	     0,   1,   2,   3,   4,   5,   6,   -,   -
// Joint Name:	  head,necT,necB,eyeR,eyeL,armL,armR,motL,motR
float curpos[] = { 248, 560, 140, 475, 270, 250, 290, 180, 180};  // Current position (units)
float setpos[] = { 248, 560, 140, 475, 270, 250, 290,   0,   0};  // Required position (units)
float curvel[] = {   0,   0,   0,   0,   0,   0,   0,   0,   0};  // Current velocity (units/sec)
float maxvel[] = { 500, 400, 500,2400,2400, 600, 600, 255, 255};  // Max Servo velocity (units/sec)
float accell[] = { 350, 300, 480,1800,1800, 500, 500, 800, 800};  // Servo acceleration (units/sec^2)



// -------------------------------------------------------------------
/// Initial setup
// -------------------------------------------------------------------

void setup() {

	// Output Enable (EO) pin for the servo motors
	pinMode(SERVO_ENABLE_PIN, OUTPUT);
	digitalWrite(SERVO_ENABLE_PIN, HIGH);

	// Communicate with servo shield (Analog servos run at ~60Hz)
	pwm.begin();
	pwm.setPWMFreq(60);

	// Turn off servo outputs
	for (int i = 0; i < NUMBER_OF_SERVOS; i++) {
		pwm.setPin(i, 0);
	}

	// Initialize serial communication for debugging
	Serial.begin(115200);
	Serial.println(F("--- Wall-E Control Sketch ---"));

	randomSeed(analogRead(0));

	// Check if servo animation queue is working, and move servos to known starting positions
	if (queue.errors()) Serial.println(F("Error: Unable to allocate memory for servo animation queue"));
	
	// Soft start the servo motors
	Serial.println(F("Starting up the servo motors"));
	digitalWrite(SERVO_ENABLE_PIN, LOW);
	playAnimation(0);
	softStart(queue.pop(), 3500);

	// If an oLED is present, start it up
	//#ifdef OLED
		Serial.println(F("Starting up the display"));
		//u8g2.begin();
		//displayLevel(100);
	//#endif

	Serial.println(F("Sartup complete; entering main loop"));
}



// -------------------------------------------------------------------
/// Read input from serial port
///
/// This function reads incoming characters in the serial port
/// and inserts them into a buffer to be processed later.
// -------------------------------------------------------------------

void readSerial() {

	// Read incoming byte
	char inchar = Serial.read();

	// If the string has ended, evaluate the serial buffer
	if (inchar == '\n' || inchar == '\r') {

		if (serialLength > 0) evaluateSerial();
		serialBuffer[0] = 0;
		serialLength = 0;

	// Otherwise add to the character to the buffer
	} else {
		if (serialLength == 0) firstChar = inchar;
		else {
			serialBuffer[serialLength-1] = inchar;
			serialBuffer[serialLength] = 0;
		}
		serialLength++;

		// To prevent overflows, evalute the buffer if it is full
		if (serialLength == MAX_SERIAL_LENGTH) {
			evaluateSerial();
			serialBuffer[0] = 0;
			serialLength = 0;
		}
	}
}



// -------------------------------------------------------------------
/// Evaluate input from serial port
///
/// Parse the received serial message which is stored in
/// the "serialBuffer" filled by the "readSerial()" function
// -------------------------------------------------------------------

void evaluateSerial() {

	// Evaluate integer number in the serial buffer
	int number = atoi(serialBuffer);

	Serial.print(firstChar); Serial.println(number);


	// Motor Inputs and Offsets
	// -- -- -- -- -- -- -- -- -- -- -- -- -- --
	if      (firstChar == 'X' && number >= -100 && number <= 100) turnValue = int(number * 2.55);       // Left/right control
	else if (firstChar == 'Y' && number >= -100 && number <= 100) moveValue = int(number * 2.55);       // Forward/reverse control
	else if (firstChar == 'S' && number >= -100 && number <= 100) turnOffset = number;                  // Steering offset
	else if (firstChar == 'O' && number >=    0 && number <= 250) motorDeadzone = int(number);          // Motor deadzone offset


	// Animations
	// -- -- -- -- -- -- -- -- -- -- -- -- -- --
	else if (firstChar == 'A') playAnimation(number);


	// Autonomous servo mode
	// -- -- -- -- -- -- -- -- -- -- -- -- -- --
	else if (firstChar == 'M' && number == 0) autoMode = false;
	else if (firstChar == 'M' && number == 1) autoMode = true;


	// Manual servo control
	// -- -- -- -- -- -- -- -- -- -- -- -- -- --
	else if (firstChar == 'L' && number >= 0 && number <= 100) {   // Move left arm
		autoMode = false;
		queue.clear();
		setpos[5] = int(number * 0.01 * (preset[5][1] - preset[5][0]) + preset[5][0]);
	} else if (firstChar == 'R' && number >= 0 && number <= 100) { // Move right arm
		autoMode = false;
		queue.clear();
		setpos[6] = int(number * 0.01 * (preset[6][1] - preset[6][0]) + preset[6][0]);
	} else if (firstChar == 'B' && number >= 0 && number <= 100) { // Move neck bottom
		autoMode = false;
		queue.clear();
		setpos[2] = int(number * 0.01 * (preset[2][1] - preset[2][0]) + preset[2][0]);
	} else if (firstChar == 'T' && number >= 0 && number <= 100) { // Move neck top
		autoMode = false;
		queue.clear();
		setpos[1] = int(number * 0.01 * (preset[1][1] - preset[1][0]) + preset[1][0]);
	} else if (firstChar == 'G' && number >= 0 && number <= 100) { // Move head rotation
		autoMode = false;
		queue.clear();
		setpos[0] = int(number * 0.01 * (preset[0][1] - preset[0][0]) + preset[0][0]);
	} else if (firstChar == 'E' && number >= 0 && number <= 100) { // Move eye left
		autoMode = false;
		queue.clear();
		setpos[4] = int(number * 0.01 * (preset[4][1] - preset[4][0]) + preset[4][0]);
	} else if (firstChar == 'U' && number >= 0 && number <= 100) { // Move eye right
		autoMode = false;
		queue.clear();
		setpos[3] = int(number * 0.01 * (preset[3][1] - preset[3][0]) + preset[3][0]);
	}
	

	// Manual Movements with WASD
	// -- -- -- -- -- -- -- -- -- -- -- -- -- --
	else if (firstChar == 'w') {		// Forward movement
		moveValue = pwmspeed;
		turnValue = 0;
		setpos[0] = (preset[0][1] + preset[0][0]) / 2;
	}
	else if (firstChar == 'q') {		// Stop movement
		moveValue = 0;
		turnValue = 0;
		setpos[0] = (preset[0][1] + preset[0][0]) / 2;
	}
	else if (firstChar == 's') {		// Backward movement
		moveValue = -pwmspeed;
		turnValue = 0;
		setpos[0] = (preset[0][1] + preset[0][0]) / 2;
	}
	else if (firstChar == 'a') {		// Drive & look left
		moveValue = 0;
		turnValue = -pwmspeed;
		setpos[0] = preset[0][0];
	}
	else if (firstChar == 'd') {   		// Drive & look right
		moveValue = 0;
		turnValue = pwmspeed;
		setpos[0] = preset[0][1];
	}


	// Manual Eye Movements
	// -- -- -- -- -- -- -- -- -- -- -- -- -- --
	else if (firstChar == 'j') {		// Left head tilt
		setpos[4] = preset[4][0];
		setpos[3] = preset[3][1];
	}
	else if (firstChar == 'l') {		// Right head tilt
		setpos[4] = preset[4][1];
		setpos[3] = preset[3][0];
	}
	else if (firstChar == 'i') {		// Sad head
		setpos[4] = preset[4][0];
		setpos[3] = preset[3][0];
	}
	else if (firstChar == 'k') {		// Neutral head
		setpos[4] = int(0.4 * (preset[4][1] - preset[4][0]) + preset[4][0]);
		setpos[3] = int(0.4 * (preset[3][1] - preset[3][0]) + preset[3][0]);
	}


	// Head movement
	// -- -- -- -- -- -- -- -- -- -- -- -- -- --
	else if (firstChar == 'f') {		// Head up
		setpos[1] = preset[1][0];
		setpos[2] = (preset[2][1] + preset[2][0])/2;
	}
	else if (firstChar == 'g') {		// Head forward
		setpos[1] = preset[1][1];
		setpos[2] = preset[2][0];
	}
	else if (firstChar == 'h') {		// Head down
		setpos[1] = preset[1][0];
		setpos[2] = preset[2][0];
	}
	

	// Arm Movements
	// -- -- -- -- -- -- -- -- -- -- -- -- -- --
	else if (firstChar == 'b') {		// Left arm low, right arm high
		setpos[5] = preset[5][0];
		setpos[6] = preset[6][1];
	}
	else if (firstChar == 'n') {		// Both arms neutral
		setpos[5] = (preset[5][0] + preset[5][1]) / 2;
		setpos[6] = (preset[6][0] + preset[6][1]) / 2;
	}
	else if (firstChar == 'm') {		// Left arm high, right arm low
		setpos[5] = preset[5][1];
		setpos[6] = preset[6][0];
	}
}



// -------------------------------------------------------------------
/// Sequence and generate animations
// -------------------------------------------------------------------

void manageAnimations() {

	// If we are running an animation
	// -- -- -- -- -- -- -- -- -- -- -- -- -- --
	if ((queue.size() > 0) && (animeTimer <= millis())) {
		// Set the next waypoint time
		animation_t newValues = queue.pop();
		animeTimer = millis() + newValues.timer;

		// Set all the joint positions
		for (int i = 0; i < NUMBER_OF_SERVOS; i++) {
			// Scale the positions using the servo calibration values
			setpos[i] = int(newValues.servos[i] * 0.01 * (preset[i][1] - preset[i][0]) + preset[i][0]);
		}


	// If we are in autonomous mode and no movements are queued, generate random movements
	// -- -- -- -- -- -- -- -- -- -- -- -- -- --
	} else if (autoMode && queue.empty() && (animeTimer <= millis())) {

		// For each of the servos
		for (int i = 0; i < NUMBER_OF_SERVOS; i++) {

			// Randomly determine whether or not to update the servo
			if (random(2) == 1) {

				// For most of the servo motors
				if (i == 0 || i == 1 || i == 5 || i == 6) {

					// Randomly determine the new position
					unsigned int min = preset[i][0];
					unsigned int max = preset[i][1];
					if (min > max) {
						min = max;
						max = preset[i][0];
					}
					
					setpos[i] = random(min, max+1);

				// Since the eyes should work together, only look at one of them
				} else if (i == 3) {

					int midPos1 = int((preset[i][1] - preset[i][0])*0.4 + preset[i][0]);
					int midPos2 = int((preset[i+1][1] - preset[i+1][0])*0.4 + preset[i+1][0]);

					// Determine which type of eye movement to do
					// Both eye move downwards
					if (random(2) == 1) {
						setpos[i] = random(midPos1, preset[i][0]);
						float multiplier = (setpos[i] - midPos1) / float(preset[i][0] - midPos1);
						setpos[i+1] = ((1 - multiplier) * (midPos2 - preset[i+1][0])) + preset[i+1][0];

					// Both eyes move in opposite directions
					} else {
						setpos[i] = random(midPos1, preset[i][0]);
						float multiplier = (setpos[i] - preset[i][1]) / float(preset[i][0] - preset[i][1]);
						setpos[i+1] = (multiplier * (preset[i+1][1] - preset[i+1][0])) + preset[i+1][0];
					}
				}

			}
		}

		// Finally, figure out the amount of time until the next movement should be done
		animeTimer = millis() + random(500, 3000);

	}
}



// -------------------------------------------------------------------
/// Manage the movement of the servo motors
///
/// @param  dt  Time in milliseconds since function was last called
///
/// This function uses the formulae:
///   (s = position, v = velocity, a = acceleration, t = time)
///   s = v^2 / (2*a)  <- to figure out whether to start slowing down
///   v = v + a*t      <- to calculate new servo velocity
///   s = s + v*t      <- to calculate new servo position
// -------------------------------------------------------------------

void manageServos(float dt) {

	bool moving = false;

	// For each of the servo motors
	for (int i = 0; i < NUMBER_OF_SERVOS; i++) {

		float posError = setpos[i] - curpos[i];

		// If position error is above the threshold
		if (abs(posError) > CONTROLLER_THRESHOLD && (setpos[i] != -1)) {

			digitalWrite(SERVO_ENABLE_PIN, LOW);
			moving = true;

			// Determine motion direction
			bool dir = true;
			if (posError < 0) dir = false;

			// Determine whether to accelerate or decelerate
			float acceleration = accell[i];
			if ((curvel[i] * curvel[i] / (2 * accell[i])) > abs(posError)) acceleration = -accell[i];

			// Update the current velocity
			if (dir) curvel[i] += acceleration * dt / 1000.0;
			else curvel[i] -= acceleration * dt / 1000.0;

			// Limit Velocity
			if (curvel[i] > maxvel[i]) curvel[i] = maxvel[i];
			if (curvel[i] < -maxvel[i]) curvel[i] = -maxvel[i];
			
			float dP = curvel[i] * dt / 1000.0;

			if (abs(dP) < abs(posError)) curpos[i] += dP;
			else curpos[i] = setpos[i];

			pwm.setPWM(i, 0, curpos[i]);

		} else {
			curvel[i] = 0;
		}
	}

	// Disable servos if robot is not moving
	// This helps prevents the motors from overheating
	if (moving) motorTimer = millis();
	else if (millis() - motorTimer >= SERVO_OFF_TIME) {
		//digitalWrite(SERVO_ENABLE_PIN, HIGH);
		for (int i = 0; i < NUMBER_OF_SERVOS; i++) {
			pwm.setPin(i, 0);
		}
	}
}



// -------------------------------------------------------------------
/// Servo "Soft Start" function
/// 
/// This function tries to start the servos up servo gently,
/// reducing the sudden jerking motion which usually occurs
/// when the motors power up for the first time.
///
/// @param  targetPos  The target position of the servos after startup
/// @param  timeMs     Time in milliseconds in which soft start should complete
// -------------------------------------------------------------------

void softStart(animation_t targetPos, int timeMs) {

	for (int i = 0; i < NUMBER_OF_SERVOS; i++) {
		if (targetPos.servos[i] >= 0) {
			curpos[i] = int(targetPos.servos[i] * 0.01 * (preset[i][1] - preset[i][0]) + preset[i][0]);

			unsigned long endTime = millis() + timeMs / NUMBER_OF_SERVOS;

			while (millis() < endTime) {
				pwm.setPWM(i, 0, curpos[i]);
				delay(10);
				pwm.setPin(i, 0);
				delay(50);
			}
			pwm.setPWM(i, 0, curpos[i]);
			setpos[i] = curpos[i];
		}
	}
}



// -------------------------------------------------------------------
/// Manage the movement of the main motors
///
/// @param  dt  Time in milliseconds since function was last called
// -------------------------------------------------------------------

void manageMotors(float dt) {

	// Update Main Motor Values
	setpos[NUMBER_OF_SERVOS] = moveValue - turnValue;
	setpos[NUMBER_OF_SERVOS + 1] = moveValue + turnValue;

	// Apply turn offset (motor trim) only when motors are active
	if (setpos[NUMBER_OF_SERVOS] != 0) setpos[NUMBER_OF_SERVOS] -= turnOffset;
	if (setpos[NUMBER_OF_SERVOS + 1] != 0) setpos[NUMBER_OF_SERVOS + 1] += turnOffset;

	for (int i = NUMBER_OF_SERVOS; i < NUMBER_OF_SERVOS + 2; i++) {

		float velError = setpos[i] - curvel[i];

		// If velocity error is above the threshold
		if (abs(velError) > CONTROLLER_THRESHOLD && (setpos[i] != -1)) {

			// Determine whether to accelerate or decelerate
			float acceleration = accell[i];
			if (setpos[i] < curvel[i] && curvel[i] >= 0) acceleration = -accell[i];
			else if (setpos[i] < curvel[i] && curvel[i] < 0) acceleration = -accell[i]; 
			else if (setpos[i] > curvel[i] && curvel[i] < 0) acceleration = accell[i];

			// Update the current velocity
			float dV = acceleration * dt / 1000.0;
			if (abs(dV) < abs(velError)) curvel[i] += dV;
			else curvel[i] = setpos[i];
		} else {
			curvel[i] = setpos[i];
		}

		// Apply deadzone offset
		if (curvel[i] > 0) curvel[i] += motorDeadzone;
		else if (curvel[i] < 0) curvel[i] -= motorDeadzone; 

		// Limit Velocity
		if (curvel[i] > maxvel[i]) curvel[i] = maxvel[i];
		if (curvel[i] < -maxvel[i]) curvel[i] = -maxvel[i];
	}

	// Update motor speeds
	motorL.setSpeed(curvel[NUMBER_OF_SERVOS]);
	motorR.setSpeed(curvel[NUMBER_OF_SERVOS+1]);
}



// -------------------------------------------------------------------
/// Battery level detection
// -------------------------------------------------------------------

#ifdef BAT_L
void checkBatteryLevel() {

	// Read the analogue pin and calculate battery voltage
	float voltage = analogRead(BATTERY_LEVEL_PIN) * 5 / 1024.0;
	voltage = voltage / DIVIDER_SCALING_FACTOR;
	int percentage = int(100 * (voltage - BATTERY_MIN_VOLTAGE) / float(BATTERY_MAX_VOLTAGE - BATTERY_MIN_VOLTAGE));

  // Update the oLed Display if installed
  #ifdef OLED
    //displayLevel(percentage);
  #endif

	// Send the percentage via serial
	Serial.print(F("Battery_")); Serial.println(percentage);
}
#endif



// -------------------------------------------------------------------
/// Main program loop
// -------------------------------------------------------------------

void loop() {

	// Read any new serial messages
	// -- -- -- -- -- -- -- -- -- -- -- -- -- --
	if (Serial.available() > 0){
		readSerial();
	}


	// Load or generate new animations
	// -- -- -- -- -- -- -- -- -- -- -- -- -- --
	manageAnimations();


	// Move Servos and wheels at regular time intervals
	// -- -- -- -- -- -- -- -- -- -- -- -- -- --
	if (millis() - updateTimer >= SERVO_UPDATE_TIME) {
		updateTimer = millis();

		unsigned long newTime = micros();
		float dt = (newTime - lastTime) / 1000.0;
		lastTime = newTime;

		manageServos(dt);
		manageMotors(dt);
	}


	// Update robot status
	// -- -- -- -- -- -- -- -- -- -- -- -- -- --
	if (millis() - statusTimer >= STATUS_CHECK_TIME) {
		statusTimer = millis();

		#ifdef BAT_L
			checkBatteryLevel();
		#endif
	}
}

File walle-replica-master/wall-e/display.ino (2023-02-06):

/**
 * oLED Display
 *
 * @file      display.ino
 * @brief     Draw battery level on the oLED display
 * @author    Hans Vandamme
 * @copyright MIT license
 * @version   1.0
 *
 * Code to draw the battery level indicator onto an oLED
 * display. For instructions of how to wire up the display,
 * see the README file included in this repository.
 */

//#ifdef OLED

/**
 * Draw battery level on the display
 * 
 * @param  batlevel The current battery percentage
 */
//void displayLevel(int batlevel) {

	//u8g2.firstPage();
	//do {
		//u8g2.setDrawColor(1);
		//drawSun();

		// Scale to 50% as the battery should not drop bellow that anyway
		//drawBatt10();
	//	if (batlevel > 55) drawBatt20();
	//	if (batlevel > 60) drawBatt30();
//		if (batlevel > 65) drawBatt40();
//	if (batlevel > 70) drawBatt50();
	//	if (batlevel > 75) drawBatt60();
	//	if (batlevel > 80) drawBatt70();
		//if (batlevel > 85) drawBatt80();
	//	if (batlevel > 90) drawBatt90();
		//if (batlevel > 95) drawBatt100();
	//} while ( u8g2.nextPage() );
 
//}


/**
 * Functions to draw each of the battery level bars
 */
//void drawBatt10() {
	//u8g2.drawBox(108,0,16,40);
//}

//void drawBatt20() {
	//u8g2.drawBox(96,0,7,40);
//}

//void drawBatt30() {
	//u8g2.drawBox(84,0,7,40);
//}

//void drawBatt40() {
	//u8g2.drawBox(72,0,7,40);
//}

//void drawBatt50() {
	//u8g2.drawBox(60,0,7,40);
//}

//void drawBatt60() {
//	u8g2.drawBox(48,0,7,40);
//}

//void drawBatt70() {
	//u8g2.drawBox(36,0,7,40);
//}

//void drawBatt80() {
	//u8g2.drawBox(24,0,7,40);
//}

//void drawBatt90() {
//	u8g2.drawBox(12,0,7,40);
//}

//void drawBatt100() {
	//u8g2.drawBox(0,0,7,40);
//}


/**
 * Draw the sun icon on the display
 */
//void drawSun() {
//	u8g2.drawDisc(20, 55, 3);
//	u8g2.drawLine(20,50,20,46);
//	u8g2.drawLine(20,60,20,64);
//	u8g2.drawLine(15,55,11,55);
//	u8g2.drawLine(25,55,29,55);
//	u8g2.drawLine(22,54,25,47);
//	u8g2.drawLine(25,53,29,50);   
//u8g2.drawLine(16,53,12,50);
//	u8g2.drawLine(18,51,16,47);
//	u8g2.drawLine(16,58,12,60);
//	u8g2.drawLine(18,60,16,63);
//u8g2.drawLine(25,58,29,60);
//	u8g2.drawLine(22,60,25,63);
//}
//
//#endif /* OLED */

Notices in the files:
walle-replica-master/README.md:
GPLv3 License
